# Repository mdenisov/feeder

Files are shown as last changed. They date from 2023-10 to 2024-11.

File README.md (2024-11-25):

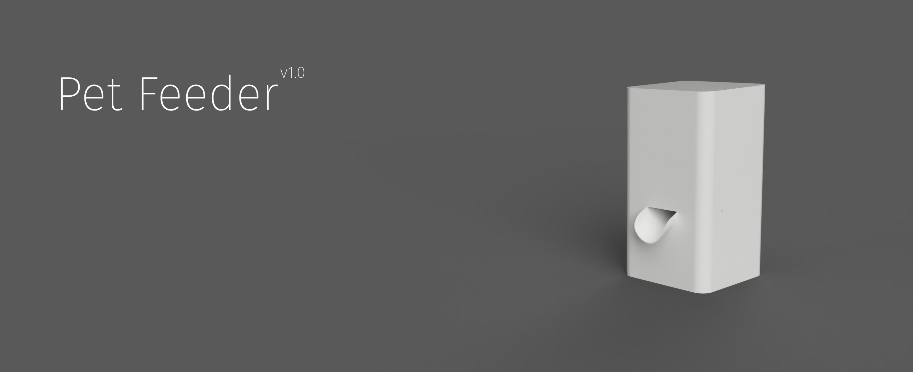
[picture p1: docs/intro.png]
Pet Feeder


# Pet Feeder

Smart feeder for pets. Works according to schedule. Supports Wifi and MQTT. WiFi remote based on ESP8266.

## Features
- Scheduled feeding
- Supports WiFi
- Supports MQTT
- Possibility of integration with a smart home

## Web Server

Feeder settings are always available on the device web page `http://feeder.local`.

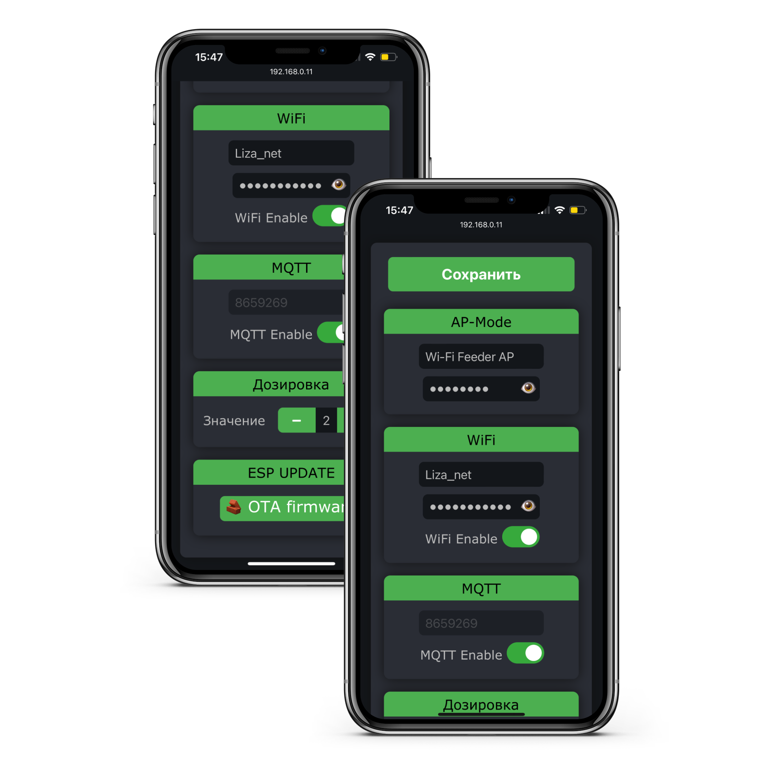
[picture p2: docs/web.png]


## Assembled device
The **STL** folder contains all the files necessary for printing.

### Reductor
Reductor designed for stepper motor **Nema 17**.
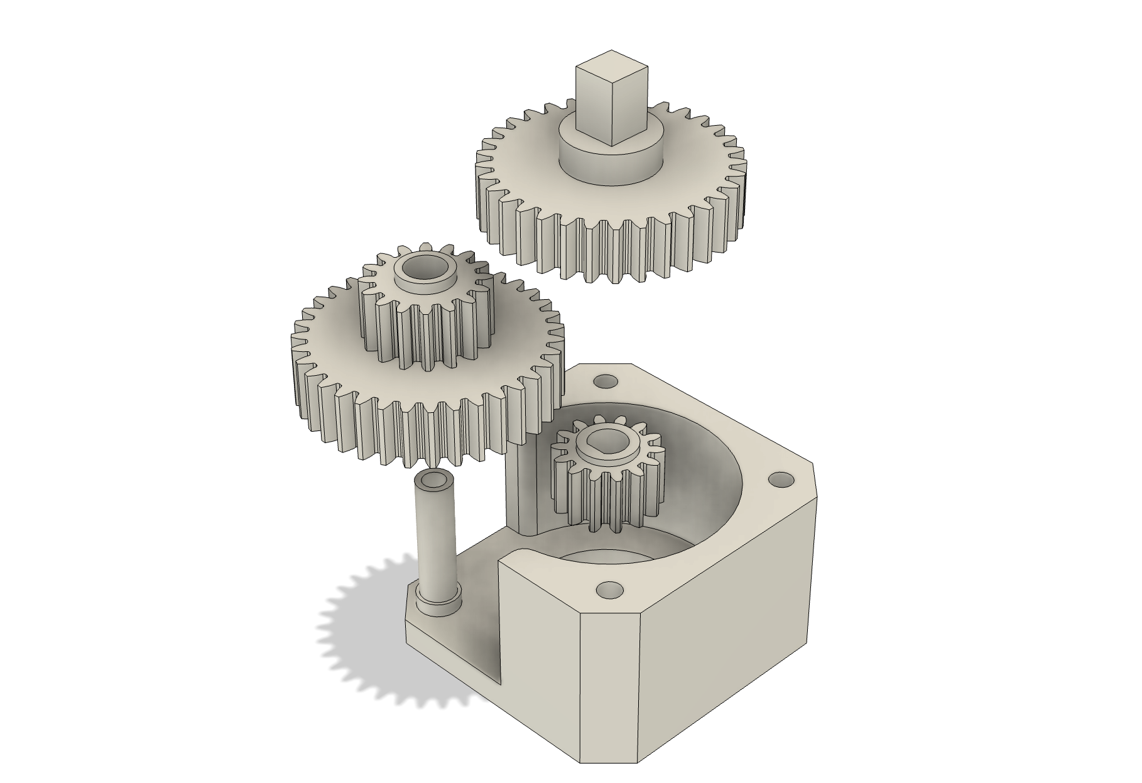
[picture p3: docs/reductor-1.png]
reductor

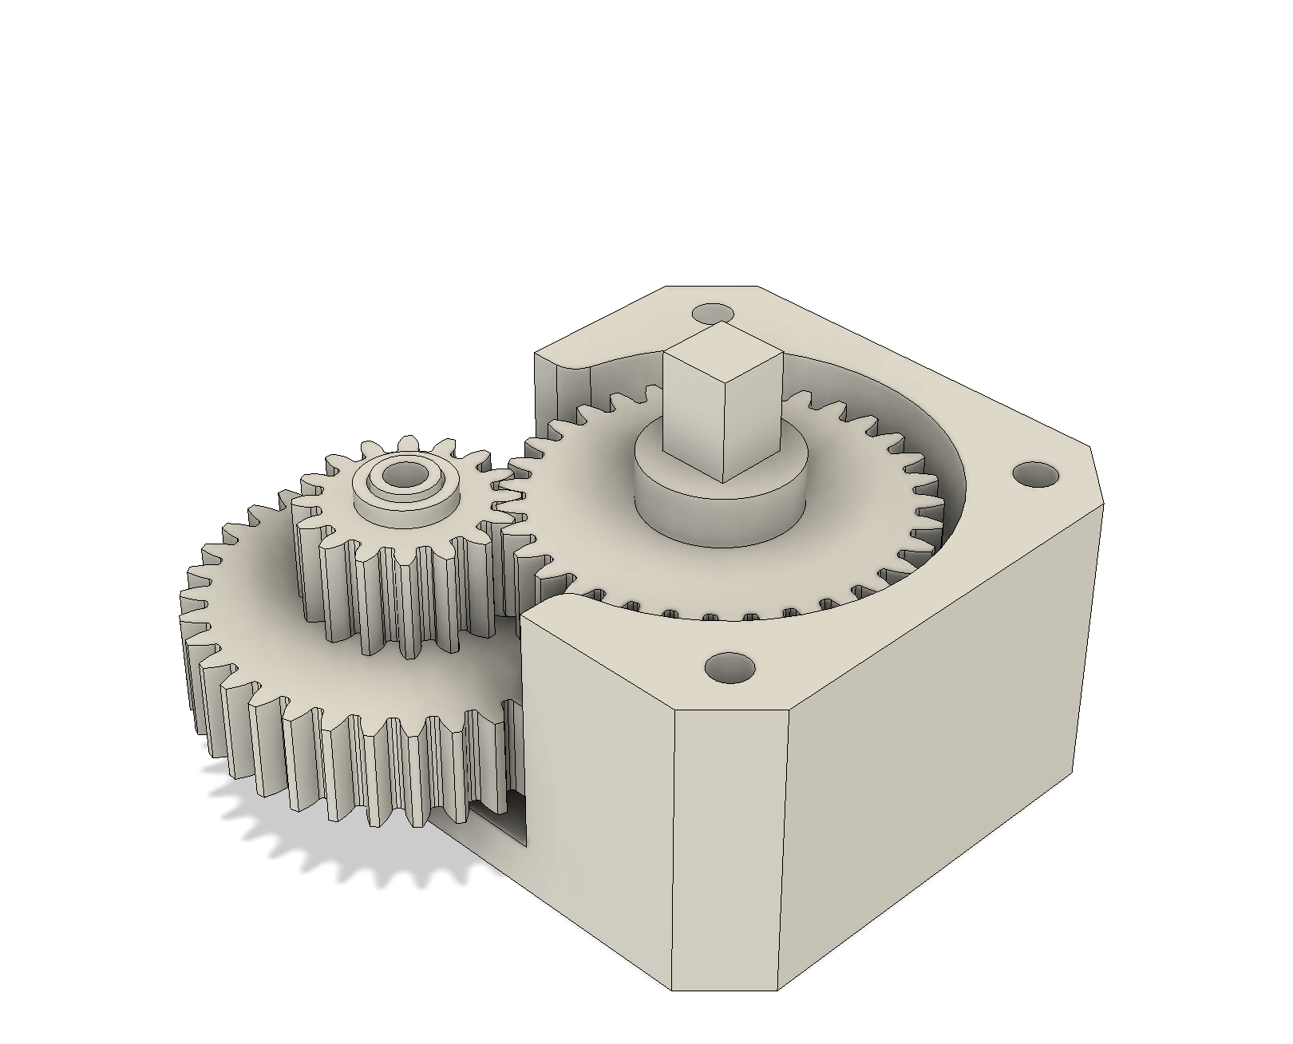
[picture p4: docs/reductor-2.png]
reductor

Use M3x30 countersunk screws to attach the reduction box to the assembly.

### Case
Step 1
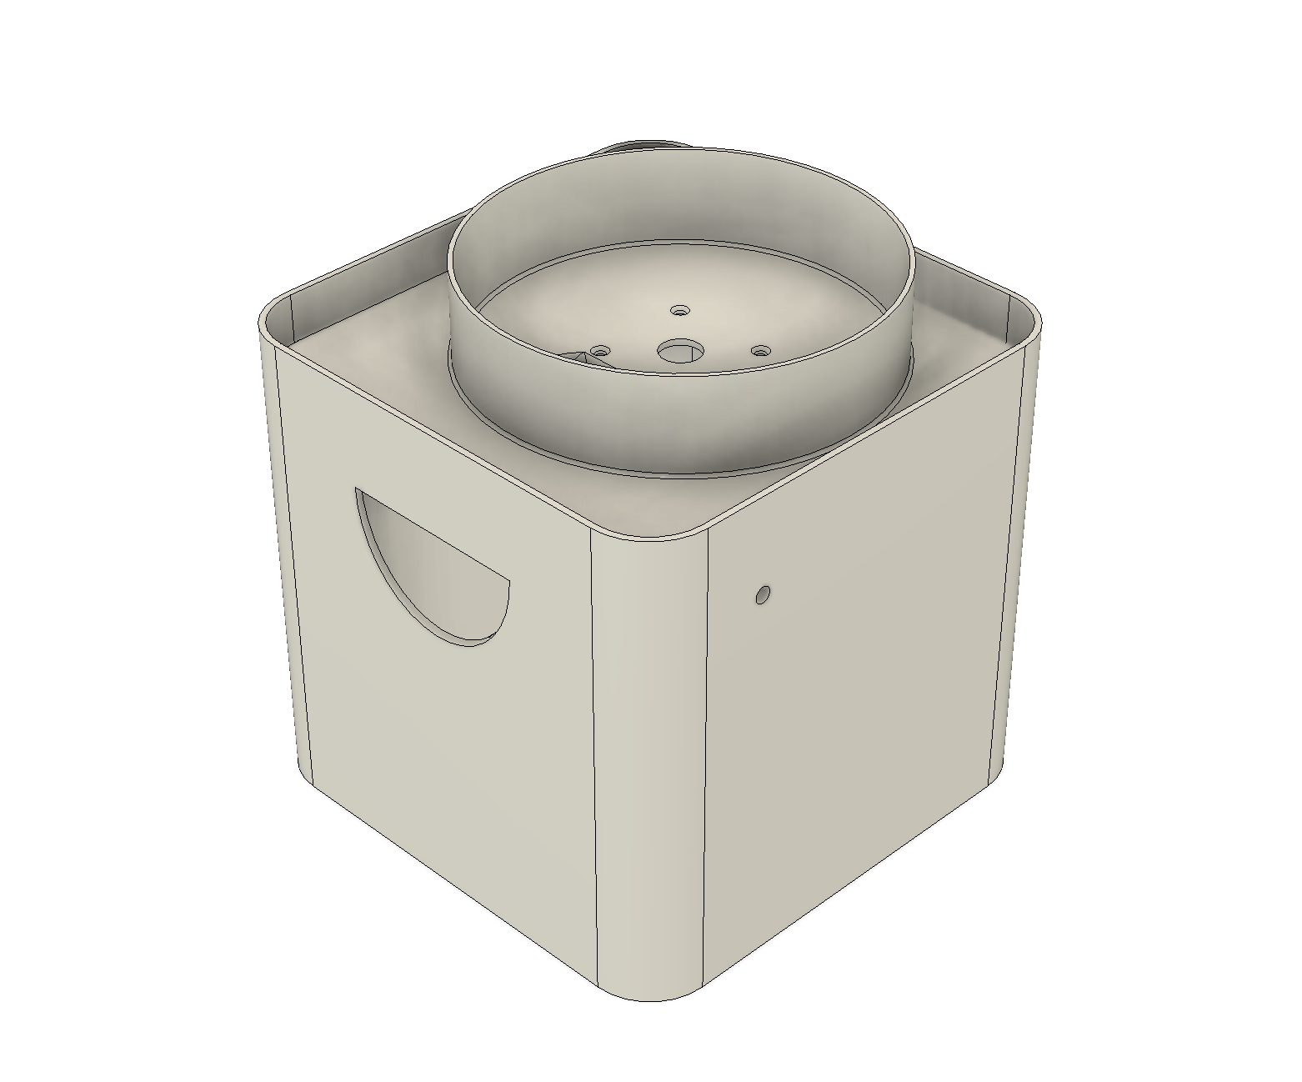
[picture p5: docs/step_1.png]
step_1

Step 2
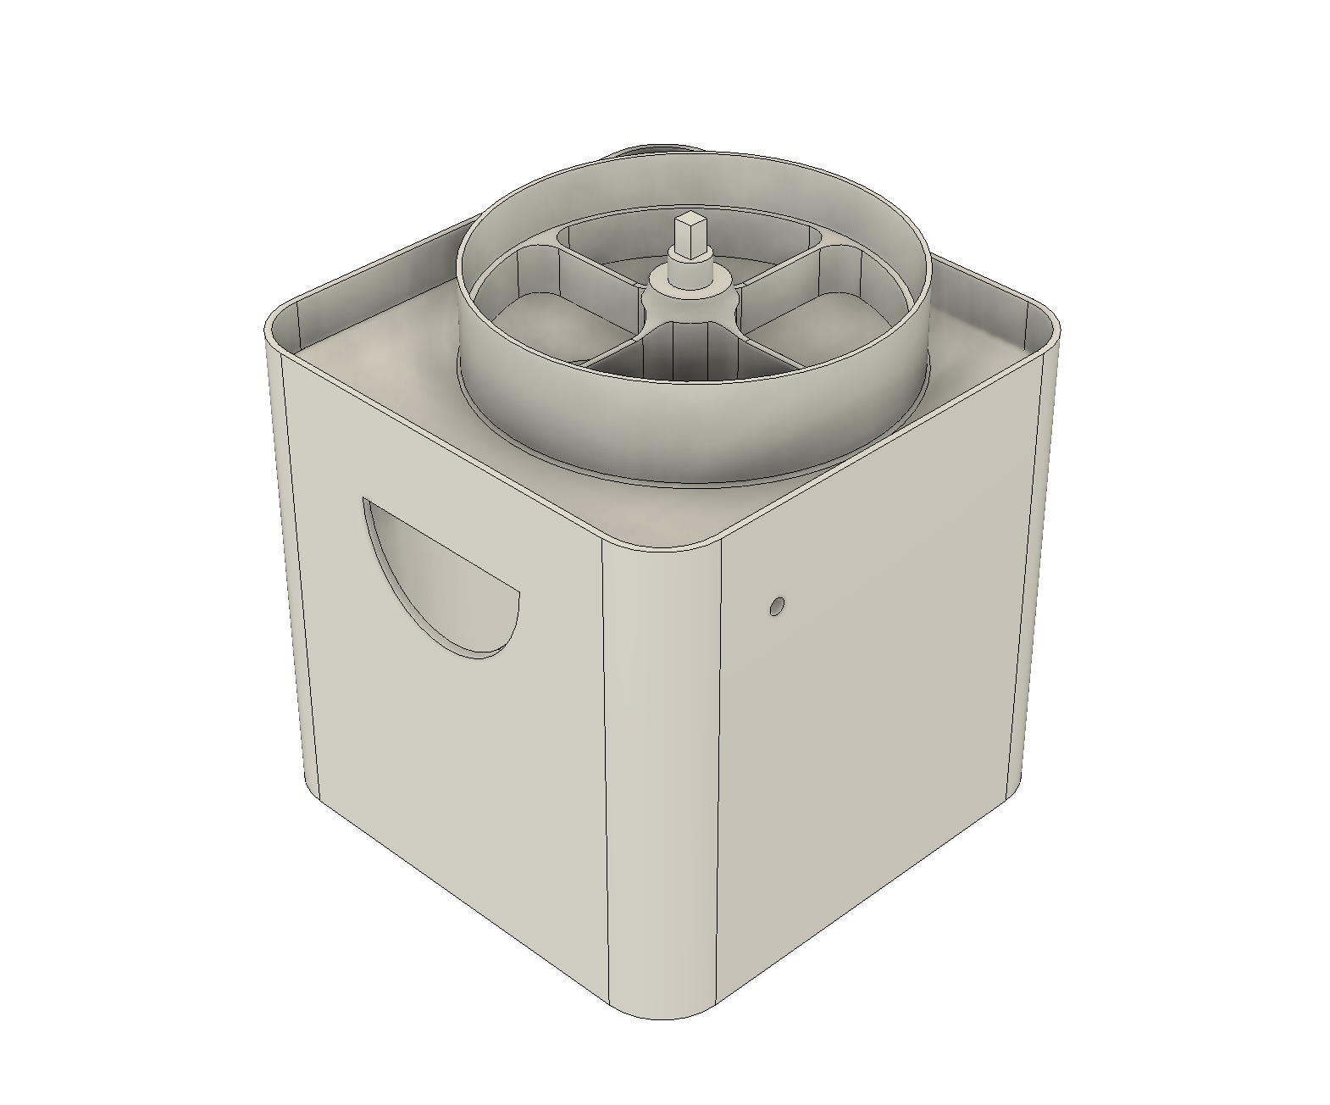
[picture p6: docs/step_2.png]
step_2

Step 3
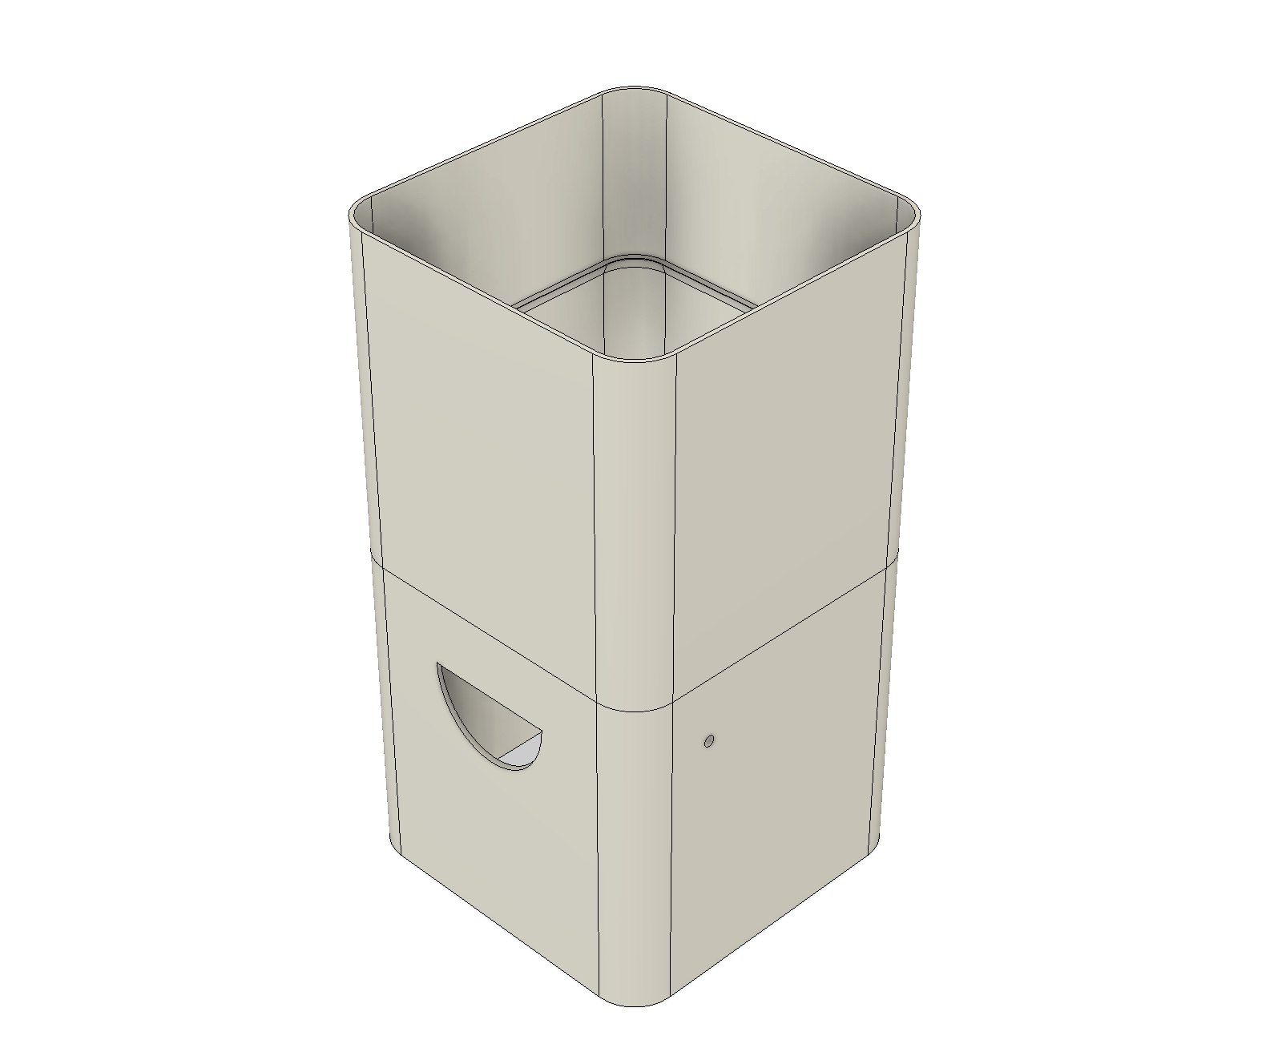
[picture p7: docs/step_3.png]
step_3

Step 4
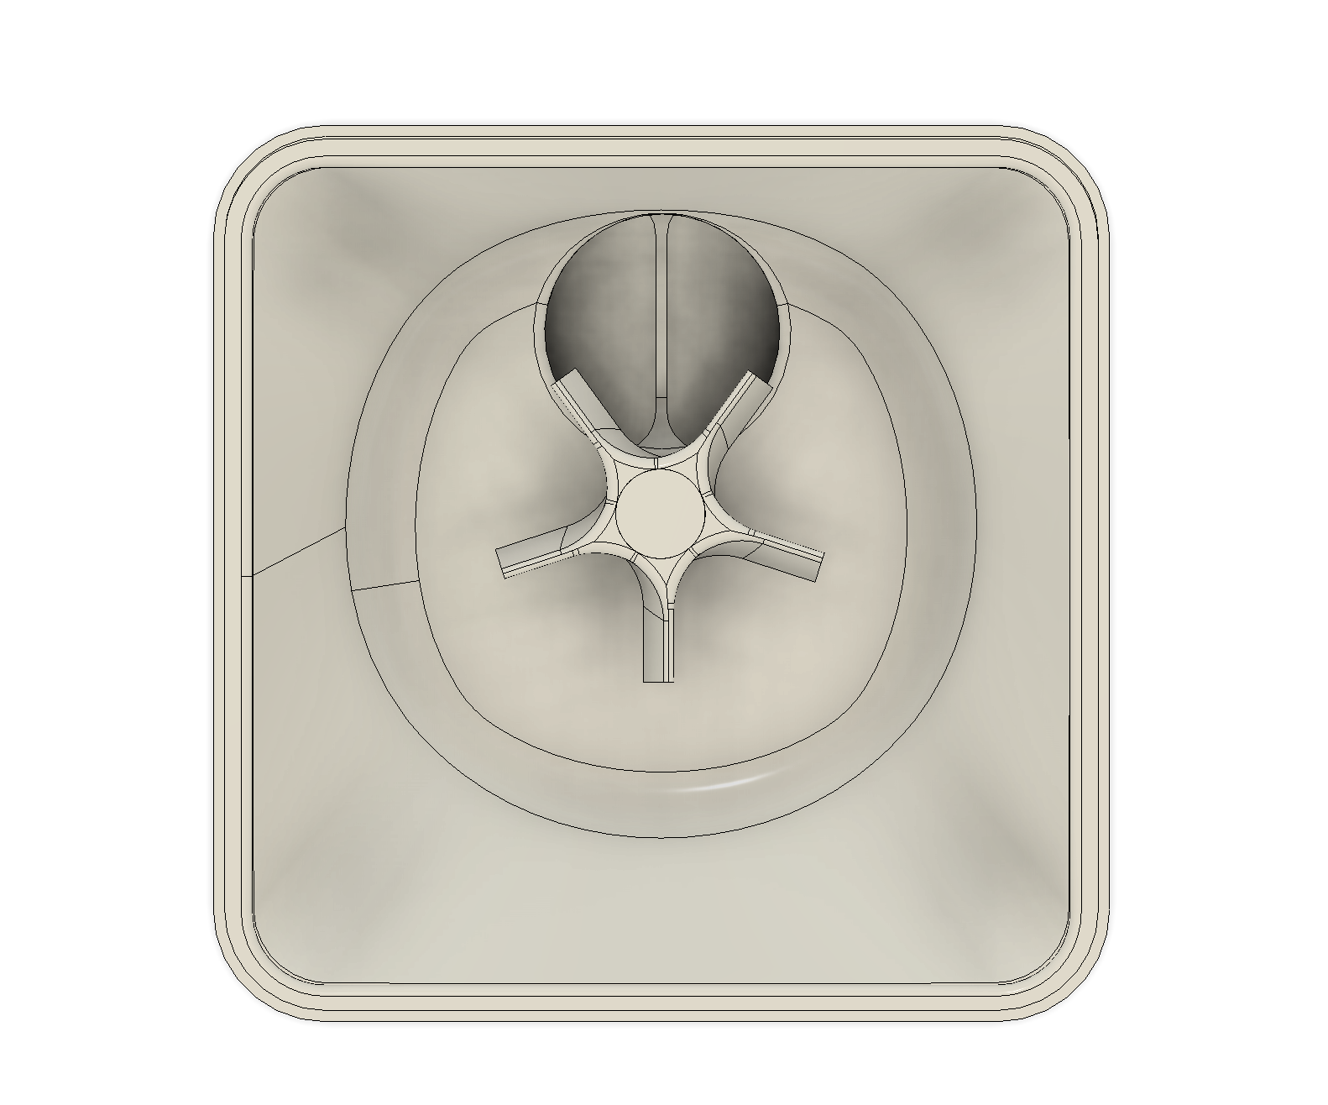
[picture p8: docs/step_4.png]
step_4

Step 5
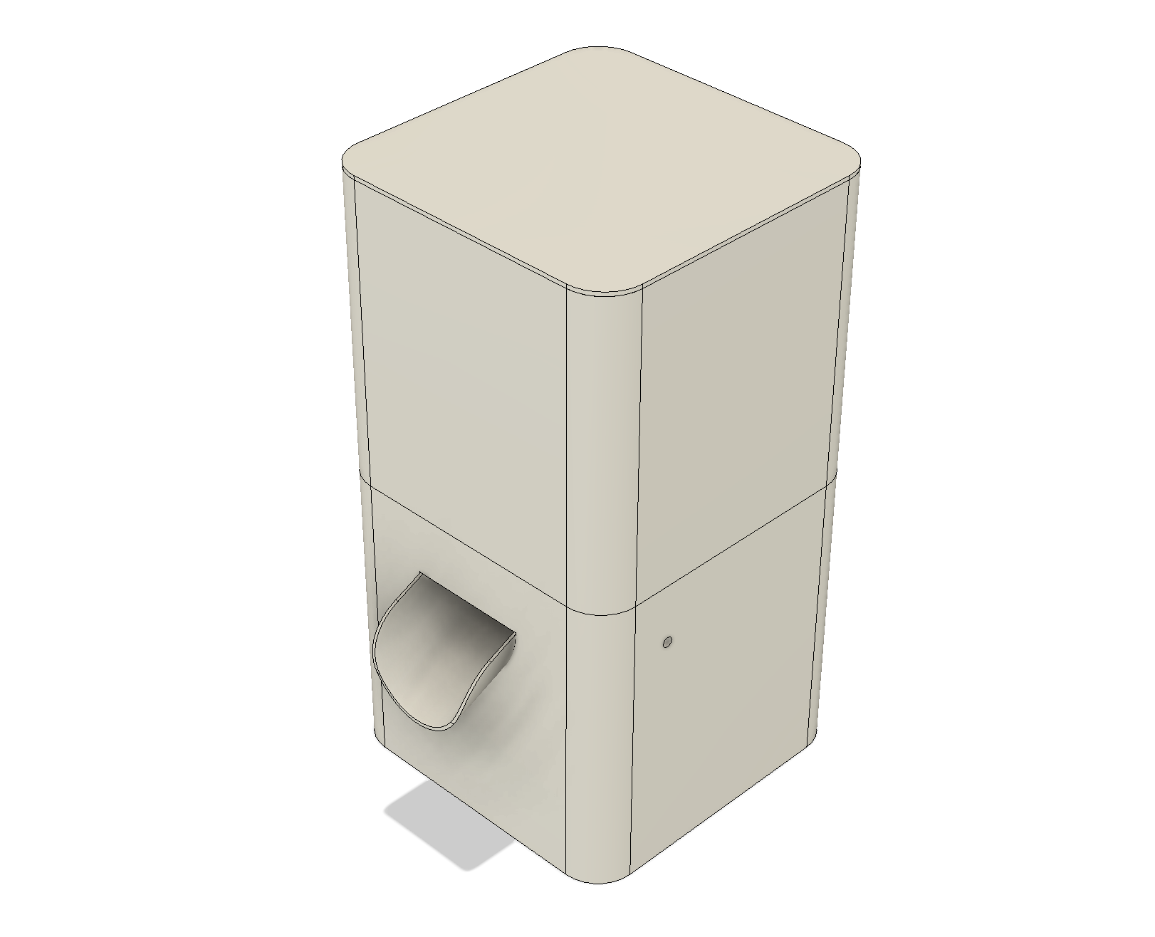
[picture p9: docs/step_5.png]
step_5

Slice
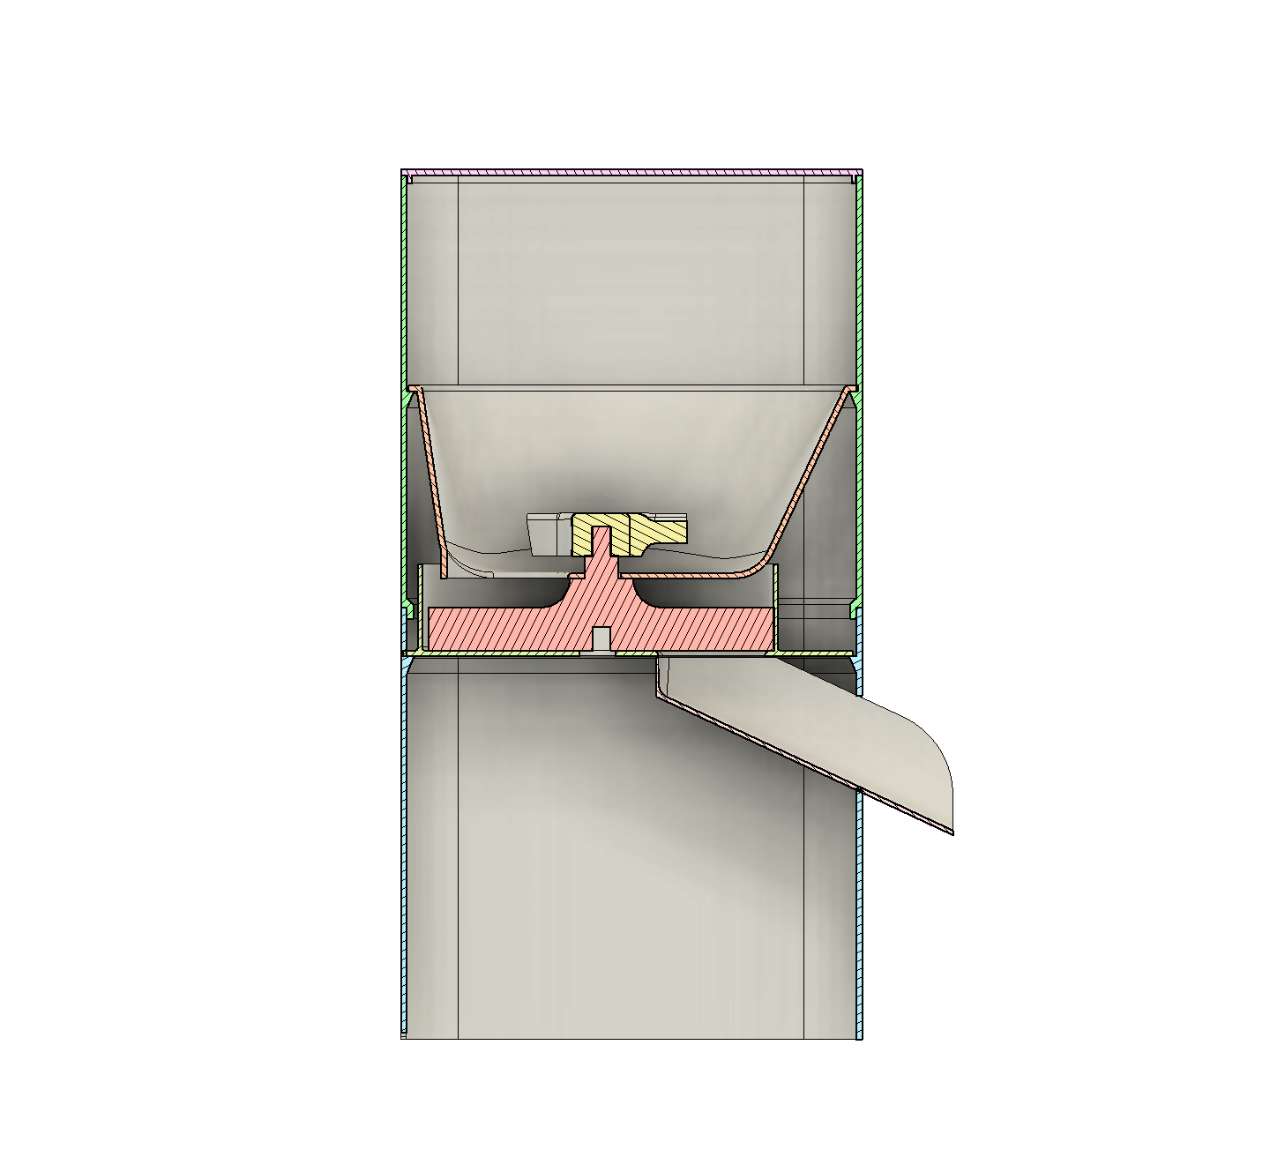
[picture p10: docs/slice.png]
slice

Final
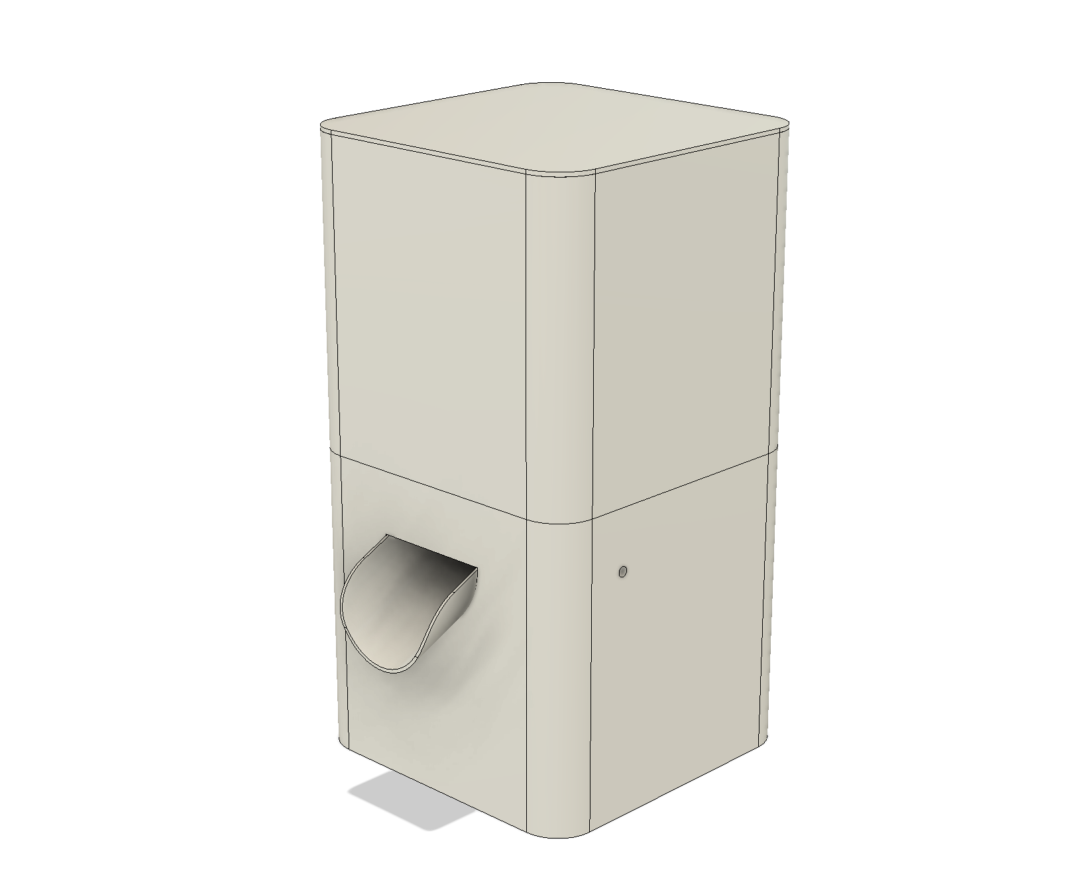
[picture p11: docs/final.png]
final


## PCB

In the **PCB** folder you will find everything you need to produce a printed circuit board.

### Main components are:

- ESP8266 (ESP-12F)
- Stepper driver A4988
- MP2307DN
- Inductor 10uH (0630; L7.0; W6.6)
- Pair diodes SS34 (SOD-123; L2.7; W1.6)
- Switch (TA-03)
- Pair JST connectors (2.0mm)
- Screw connector (KF128-2.54)
- Resistors and capacitors (0805)

And
- [Button TTP223](https://aliexpress.ru/item/32451378348.html?sku_id=66500187744)
- [Motor Nema 17](https://aliexpress.ru/item/32665922113.html?sku_id=65715688198)
- [Led](https://aliexpress.ru/item/1005004515135362.html?sku_id=12000029436349109)
- [JST Connectors](https://aliexpress.ru/item/4000091077742.html?sku_id=10000000242277758)

Final view of the printed circuit board:
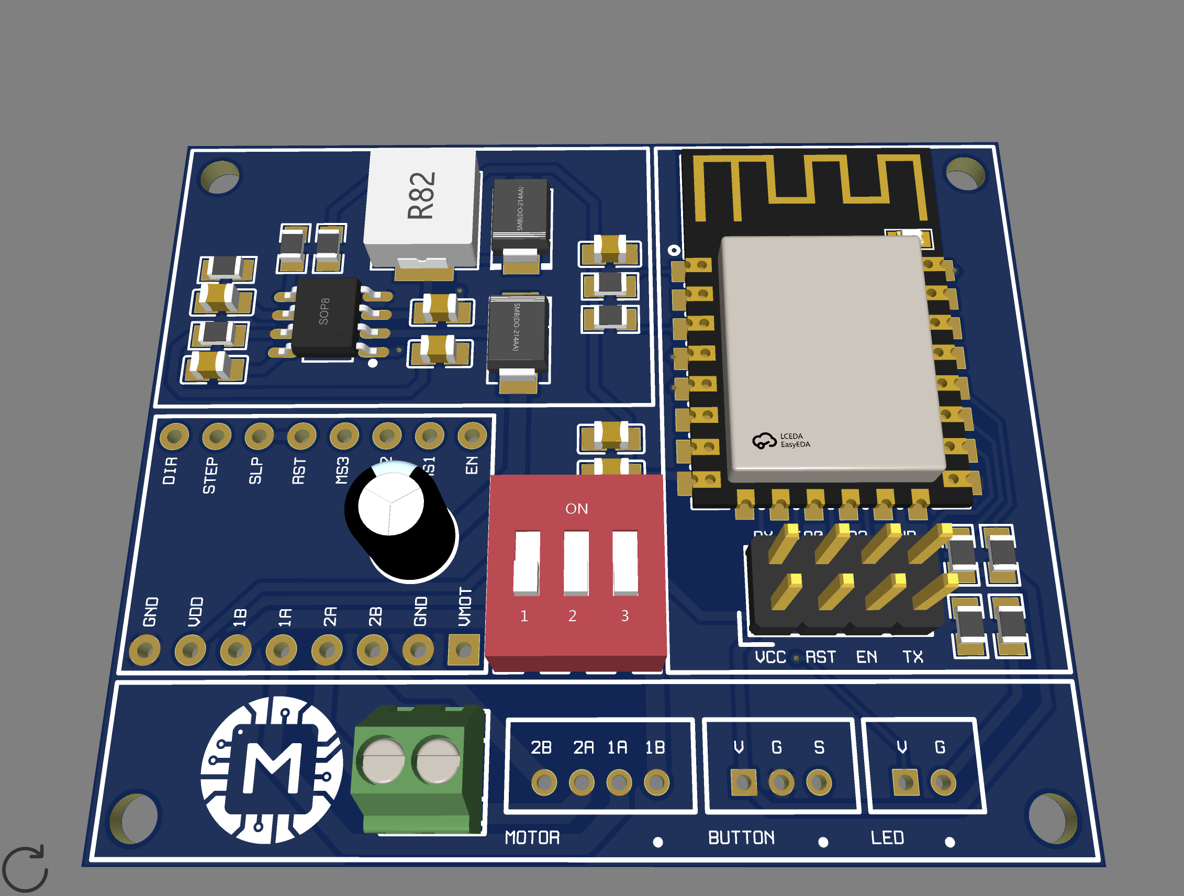
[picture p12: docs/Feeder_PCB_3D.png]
pcb


Thanks [@AlexGyver](https://github.com/AlexGyver) for awesome [libs](https://github.com/GyverLibs).

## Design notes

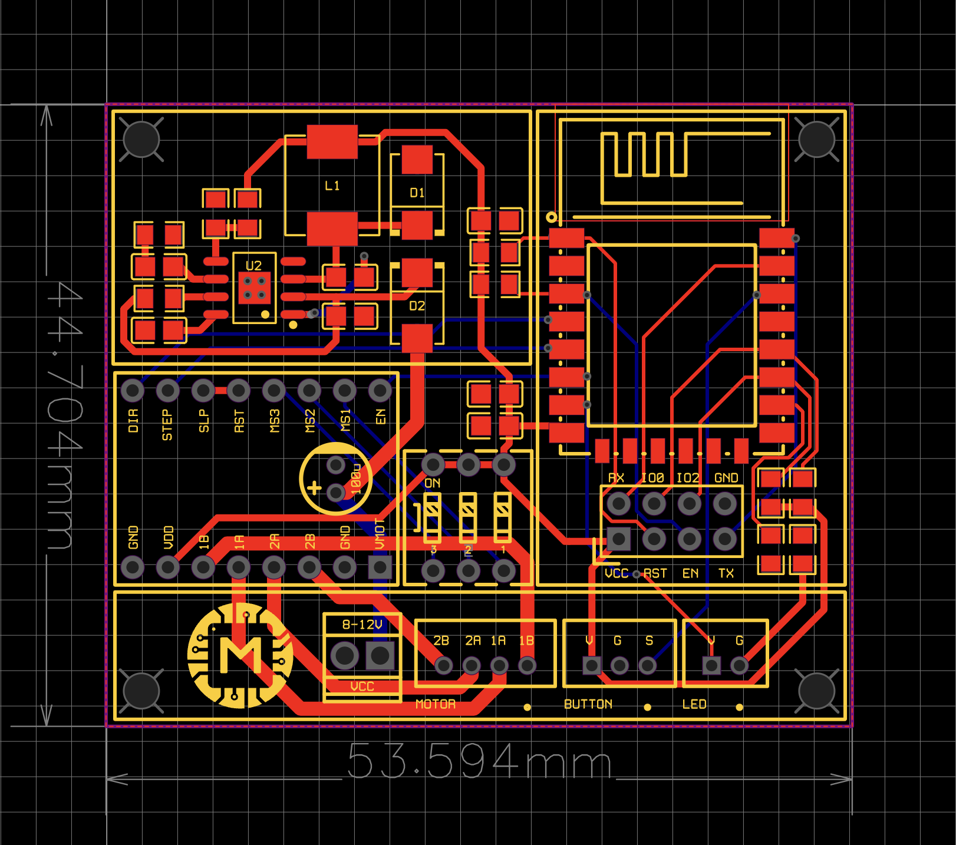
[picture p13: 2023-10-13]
docs/Feeder_PCB.png

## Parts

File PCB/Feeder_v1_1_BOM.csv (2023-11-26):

ID | Name | Designator | Footprint | Quantity | Manufacturer Part | Manufacturer | Supplier | Supplier Part
1 | MBR0530T3G | D1,D6 | SOD-123_L2.7-W1.6-LS3.7-RD-1 | 2 | MBR0530T3G | onsemi(安森美) | LCSC | C236079
2 | 100u | C1 | CAP-D5.0-F2.0 | 1
3 | 10u | C2 | C0805 | 1
4 | 100n | C3,C8 | C0805 | 2
5 | 10n | C4 | C0805 | 1
6 | 3.9n | C5 | C0805 | 1
7 | 22u | C6,C7 | C0805 | 2
8 | 1k | R6 | R0805 | 1
9 | 100k | R7 | R0805 | 1
10 | 47k | R8 | R0805 | 1
11 | 18k | R9 | R0805 | 1
12 | 6.8k | R10 | R0805 | 1
13 | 2.4GHz | U1 | WIFIM-SMD_ESP-12F-ESP8266MOD | 1 | ESP-12F(ESP8266MOD) | Ai-Thinker(安信可) | LCSC | C82891
14 | A4988 | U2 | A4988 | 1 | A4988
15 | VCC | U3 | CONN-TH_P2.54_KF128-2.54-2P | 1 | KF128-2.54-2P | KEFA(科发) | LCSC | C474920
16 | UART | U4 | UART | 1
17 | MP2307DN-LF-Z | U5 | SOP-8_L4.9-W3.9-P1.27-LS6.0-BL-EP | 1 | MP2307DN-LF-Z | MPS | LCSC | C18921
18 | 10k | R5,R4,R3,R1,R2 | R0805 | 5
19 | 10uH | L1 | IND-SMD_L7.0-W6.6_FXL0630 | 1 | FXL0624-150-M | cjiang(长江微电) | LCSC | C524609
20 | TA-03 | SW1 | SW-TH_6P-L9.2-W9.6-P2.54-LS7.62 | 1 | TA-03 | Yuandi(元迪) | LCSC | C559138
21 | LED | J1 | JST2.0_2P | 1
22 | BUTTON | J2 | JST2.0_3P | 1
23 | MOTOR | J3 | JST2.0_4P | 1

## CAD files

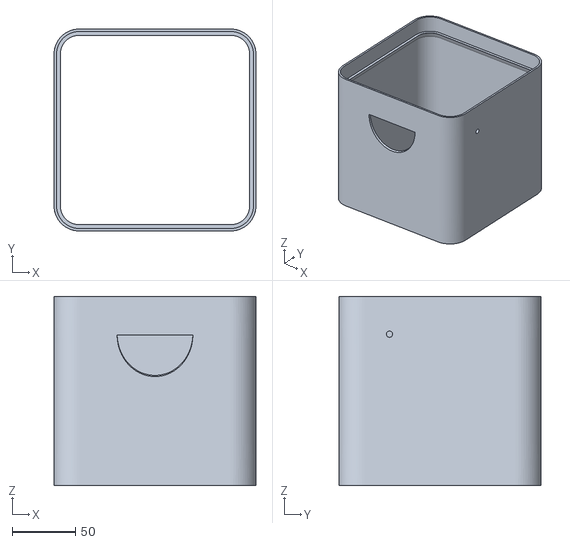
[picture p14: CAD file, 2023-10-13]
STL/box_bottom.stl
160.0 x 160.0 x 150.0

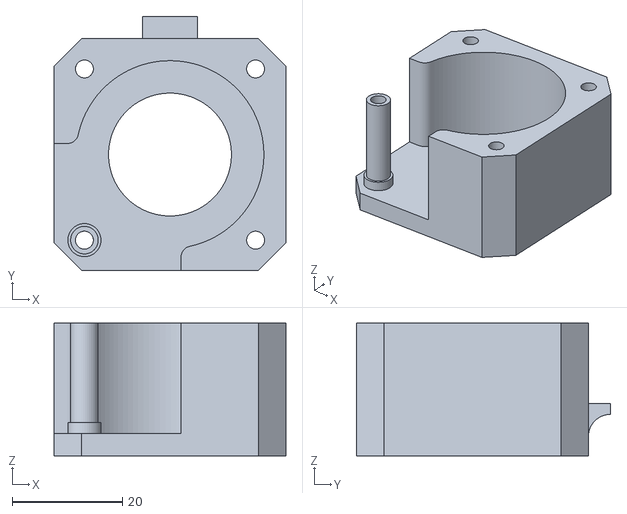
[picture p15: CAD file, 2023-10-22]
STL/reductor/reductor_box.stl
42.0 x 46.0 x 24.0

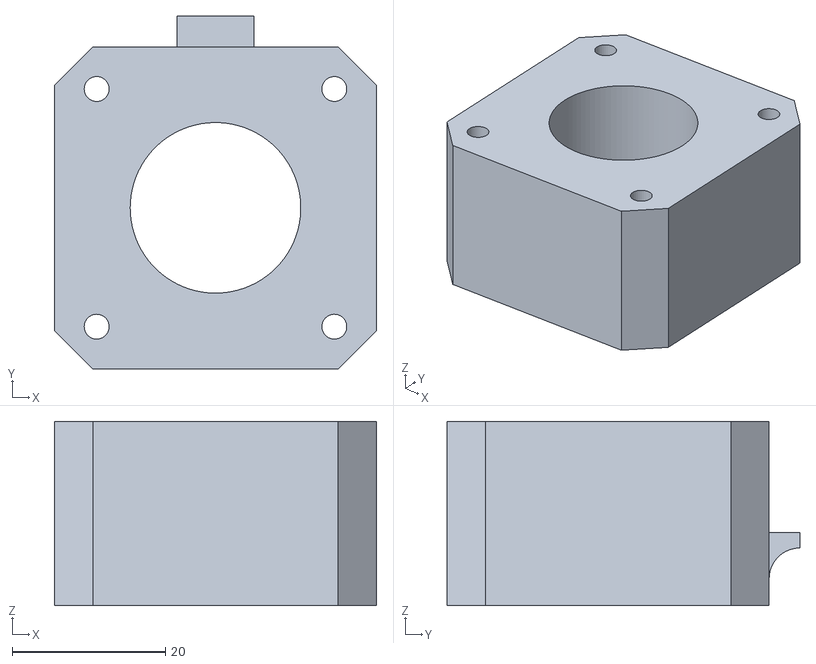
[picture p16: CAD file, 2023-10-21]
STL/without_reductor/motor_spacer.stl
42.0 x 46.0 x 24.0

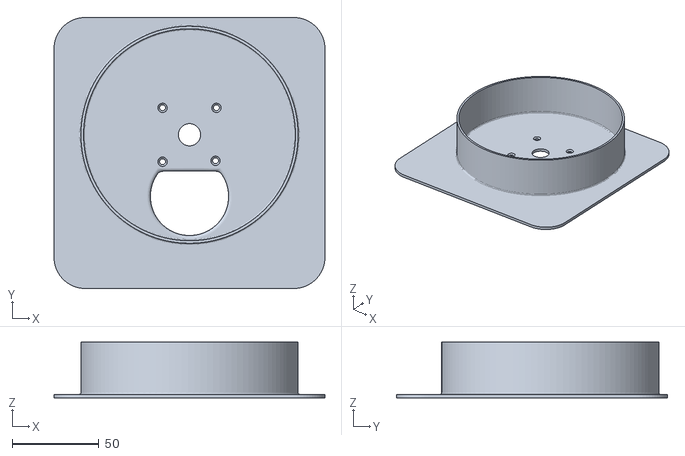
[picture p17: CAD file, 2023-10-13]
STL/box_bottom_top.stl
156.0 x 156.0 x 32.0

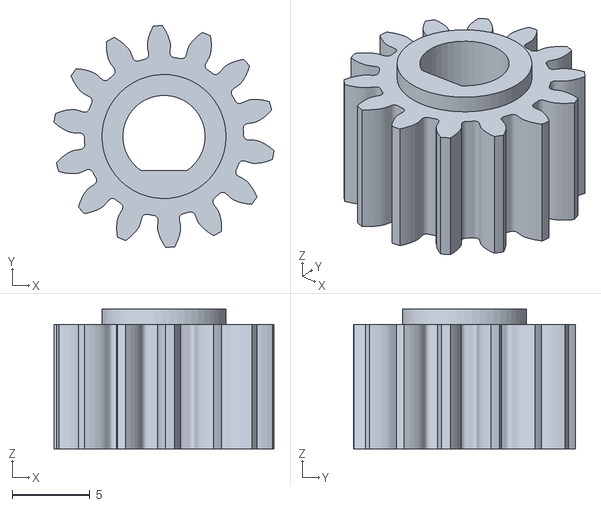
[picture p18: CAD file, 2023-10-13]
STL/reductor/reductor_gear_1.stl
14.2 x 14.3 x 9.00

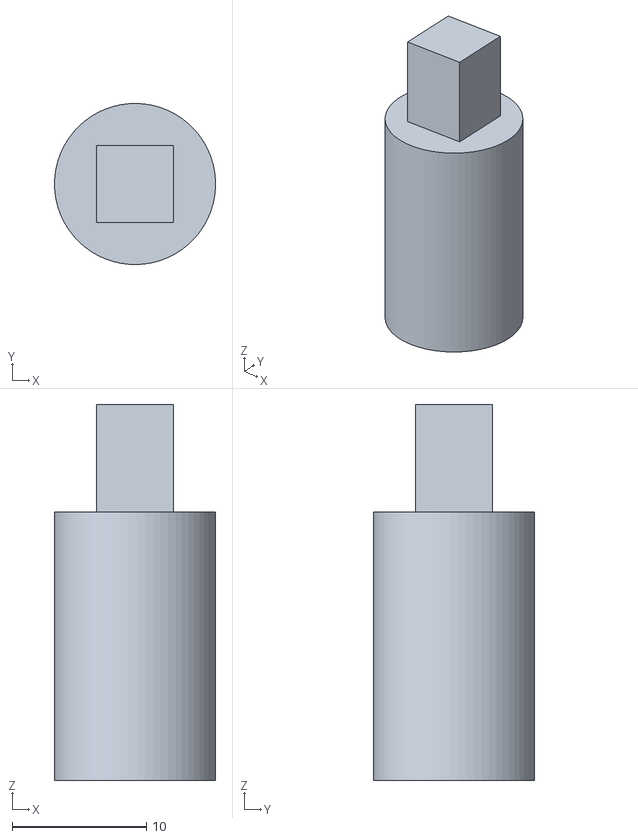
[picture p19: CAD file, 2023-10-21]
STL/without_reductor/motor_rotor.stl
12.0 x 12.0 x 28.0

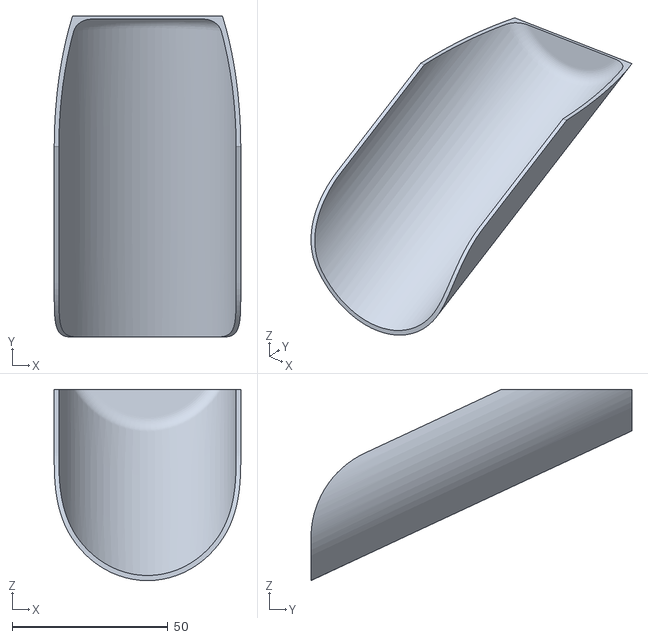
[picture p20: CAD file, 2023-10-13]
STL/box_bottom_gutter.stl
60.0 x 103.2 x 61.5

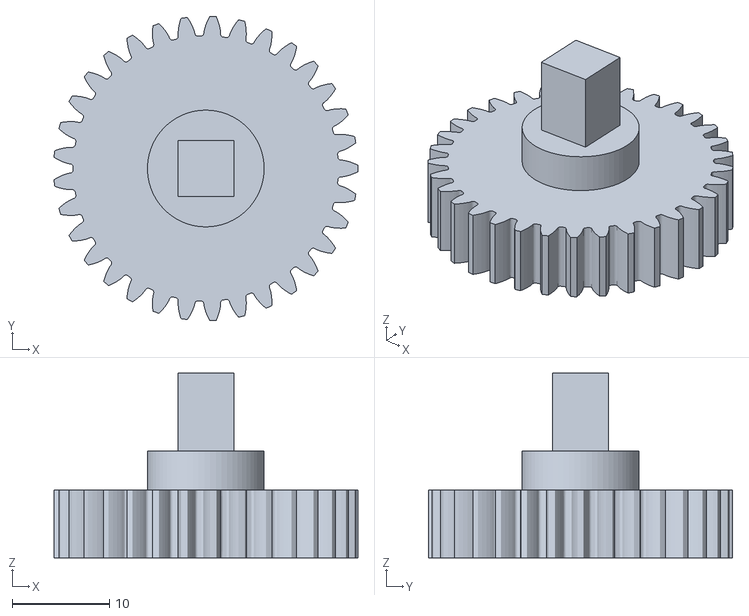
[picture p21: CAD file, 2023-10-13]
STL/reductor/reductor_gear_3.stl
31.2 x 31.3 x 19.0

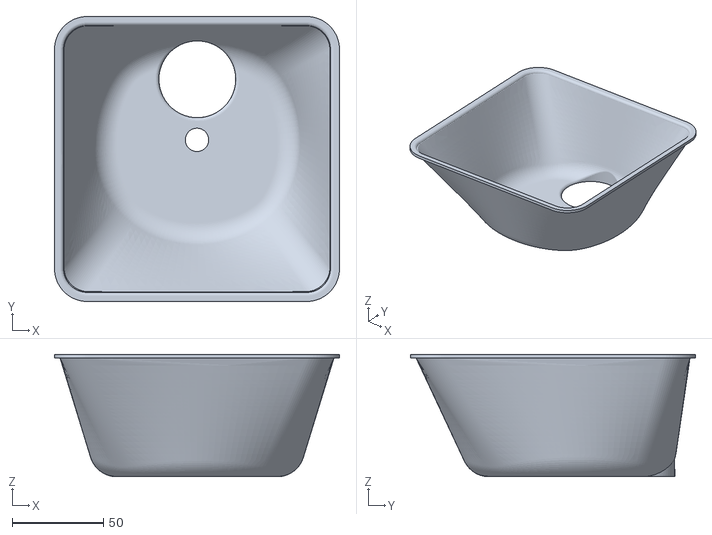
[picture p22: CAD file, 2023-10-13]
STL/box_top_crater.stl
156.0 x 156.0 x 67.0

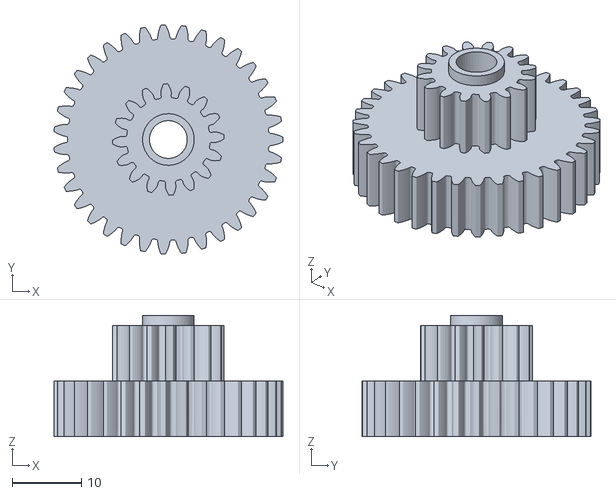
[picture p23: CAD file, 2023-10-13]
STL/reductor/reductor_gear_2.stl
33.0 x 33.1 x 17.5

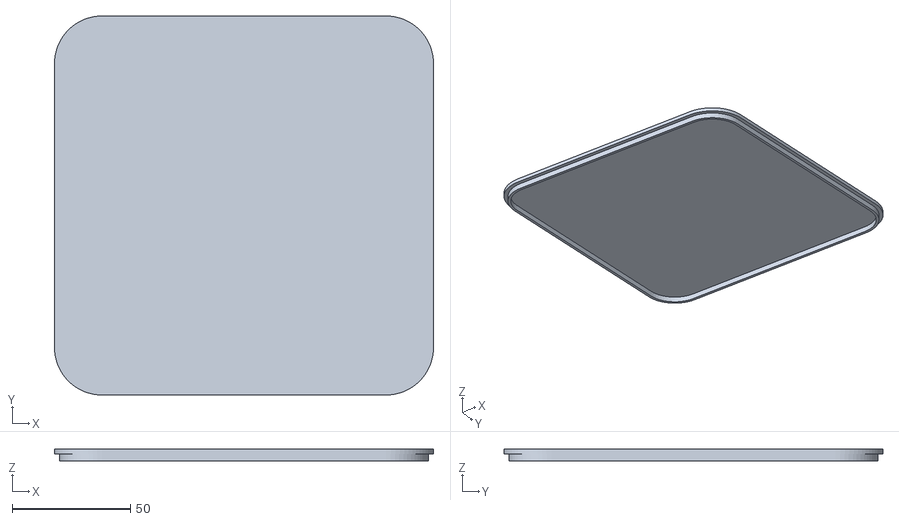
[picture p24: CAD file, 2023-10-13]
STL/box_top_cover.stl
160.0 x 160.0 x 5.00

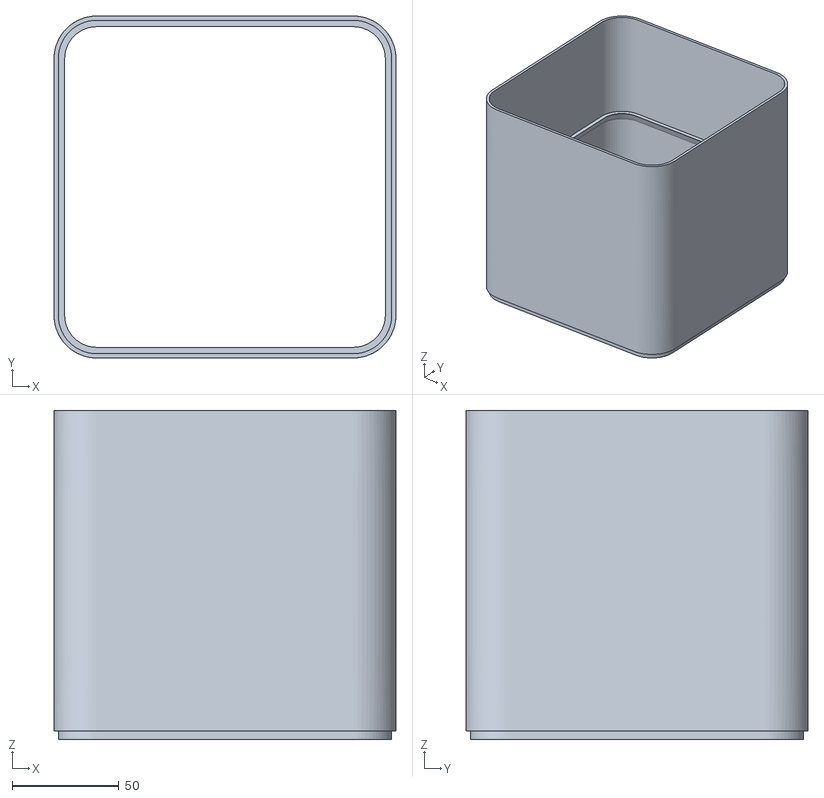
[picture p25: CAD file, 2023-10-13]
STL/box_top.stl
160.0 x 160.0 x 154.0

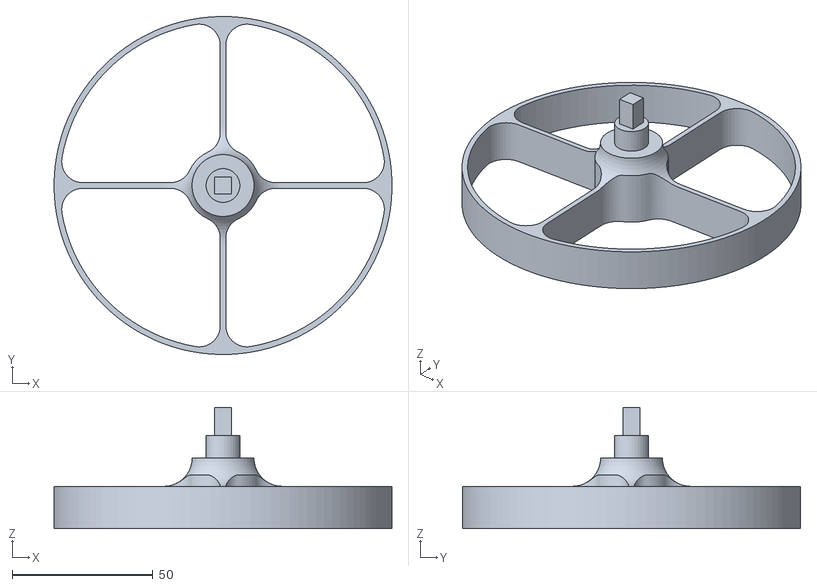
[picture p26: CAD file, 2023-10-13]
STL/box_bottom_rotor.stl
120.0 x 120.0 x 43.0

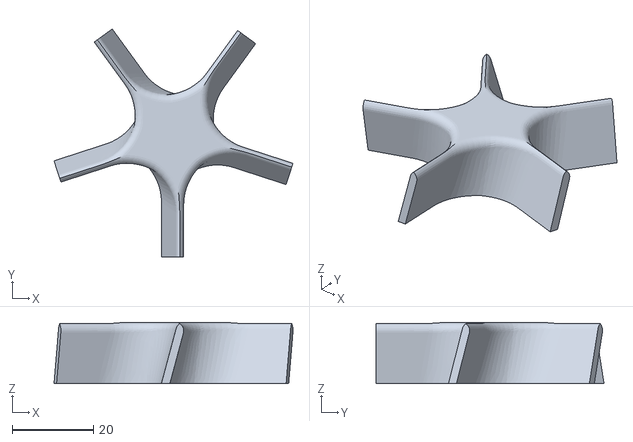
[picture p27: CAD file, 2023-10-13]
STL/box_top_screw.stl
58.8 x 56.1 x 15.0

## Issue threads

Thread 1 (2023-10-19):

Missing CPL file for PCB ordering

maksm, 2023-10-19:
Hey great project, really want to try it out, but this is my first time doing custom PCBs. I wanted to order your design on JLCPCB but in the process the BOM and CPL files are required and here in the repo only the BOM is present - could you also provide the CPL file? I have no idea what it does.

Thanks in advance and cheers for the project.

mdenisov, 2023-10-20:
@maksm Hi! To order a PCB for JLCPCB, use the included [Gerber](https://github.com/mdenisov/feeder/blob/main/PCB/Feeder_v1_0_Gerber.zip) file for upload in [order page](https://cart.jlcpcb.com/quote). I don`t have a CPL file, sorry. If you tell me how to do it, I'll do it no problem.

maksm, 2023-10-22:
@mdenisov Hey, yeah I forgot to mention that I wanted the PCB assembly also done, without it only the provided file is ok. But if I wanted to also do the PCB assembly I get to an interface where I have to provide the BOM and CPL files for the project, and am not really sure what those are.

Here is some more info when googling: https://jlcpcb.com/help/article/81-How-to-generate-the-BOM-and-Centroid-file-from-KiCAD

If I can provide any more input or help just let me know!

mdenisov, 2023-10-22:
@maksm oh, maybe you mean the element positioning file. I was able to export something like [this](https://github.com/mdenisov/feeder/blob/main/PCB/Feeder_v1_0_POS.csv). This is similar to your examples шт KiCAD.

If you need anything else, just tell me!

maksm, 2023-10-23:
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

Hey tried with the specified file, I get this error now.

```
Error

The below parts won't be assembled due to data missing.
U5,SW1,C1,C2,C3,C4,C5,C6,C7,C8,R1,R2,R3,R4,R5,R6,L1,R7,R8,J1,R9,J2,J3,D1,D2,R11,U1,U2,U3,U4 designators don't exist in the BOM file.
18K,10UH,BUTTON,3.9N,47K,UART,A4988,100N,LED,10K,100K,10N,MP2307DN-LF-Z,2.4GHZ,6.8K,100U,22U,10U,VCC,MOTOR,1K,SS34LB,TA-03,NAME FOOTPRINT QUANTITY designators don't exist in the CPL file.
```

mdenisov, 2023-10-23:
Hi 👋 Try with updated [BOM](PCB/Feeder_v1_0_BOM.csv) file. I think the error is due to a mismatch in the BOM file and Gerber file.

maksm, 2023-10-23:
Looking good now, will order 5pcs soon and report when I will assemble the unit. Might take a while :)

Thanks for all the assistance!

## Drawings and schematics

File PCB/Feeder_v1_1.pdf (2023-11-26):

MOTOR | CPU

## PULLUP

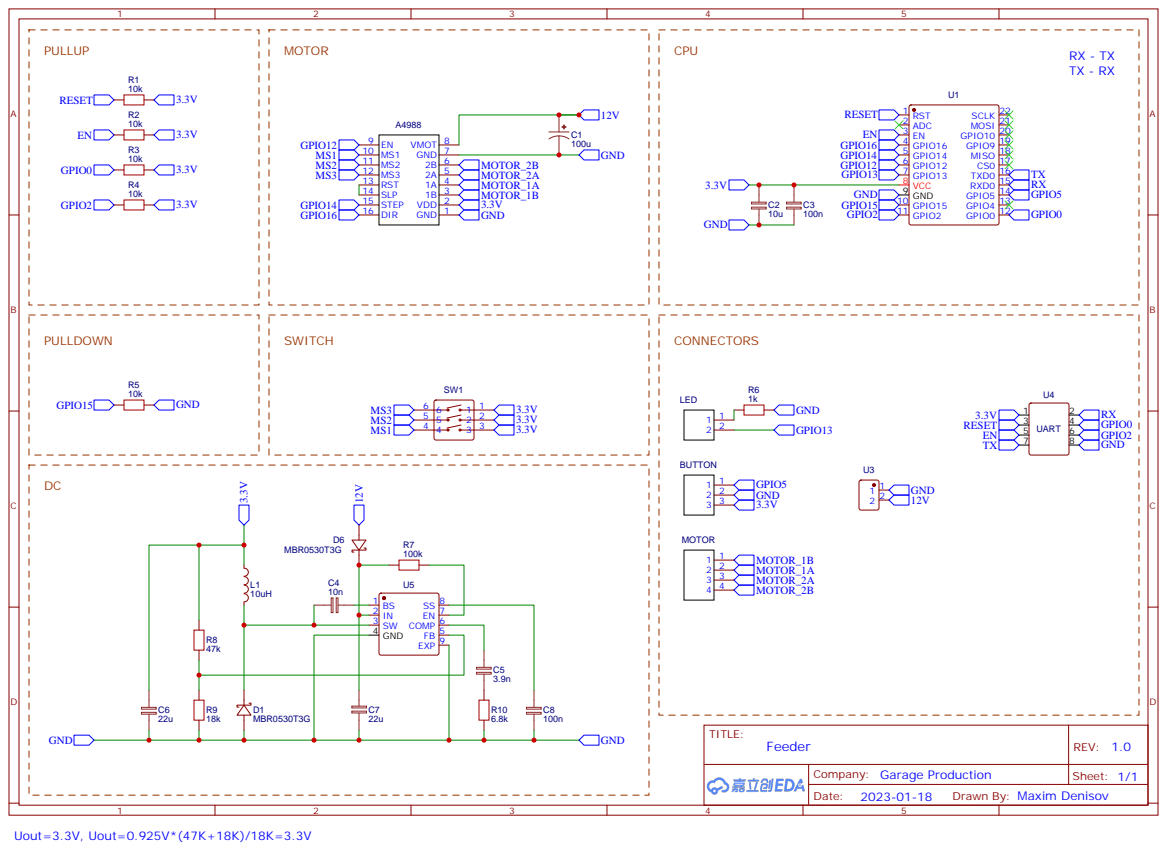
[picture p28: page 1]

Drawn By: Maxim Denisov

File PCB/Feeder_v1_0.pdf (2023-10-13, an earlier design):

MOTOR | CPU

## PULLUP

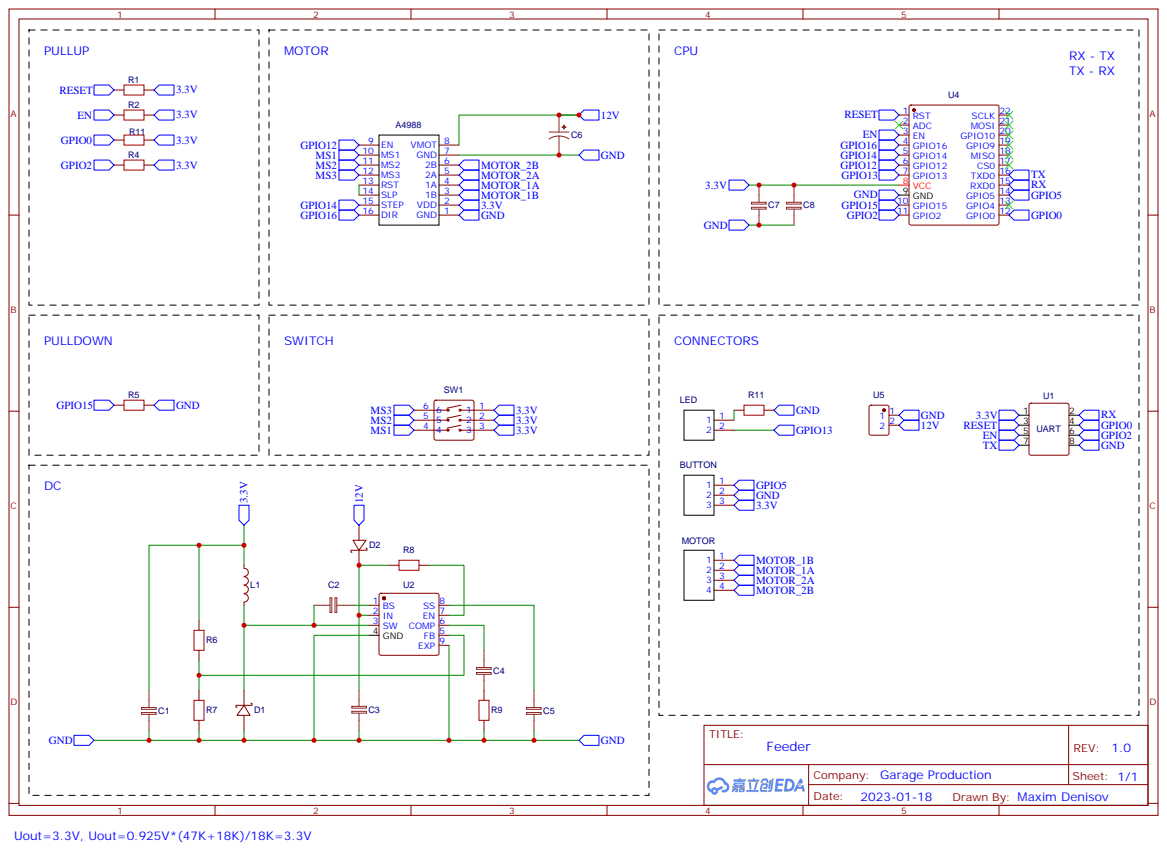
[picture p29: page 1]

Drawn By: Maxim Denisov

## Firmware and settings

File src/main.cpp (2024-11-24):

#include "env.h"

/* ================== Libs =================== */
#include <Arduino.h>
#include <EncButton.h>
#include "Led.h"

#include "config.h"
#include "utils.h"
#include "wifi-manager.h"
#include "mqtt-manager.h"
#include "eeprom-manager.h"
#include "ntp-manager.h"
#include "stepper-manager.h"
#include "schedule-manager.h"
#include "web-server.h"

/* ================ Objects ================== */
Button btn(BTN_PIN, INPUT_PULLUP, HIGH);
Led led(LED_PIN);

/* ================== Main =================== */
void setup()
{
#ifdef DEBUG_MODE
  Serial.begin(115200);
#endif

  pinMode(BTN_PIN, INPUT_PULLUP);

  led.begin();
  led.on();
  initEEPROM();
  initWifi();
  initMQTT();
  initNTP();
  initStepper();
  initSchedule();
  initUI();
}

void loop()
{
  btn.tick();
  led.tick();
  loopNTP();
  loopMQTT();
  loopStepper();
  loopSchedule();
  loopUI();

  if (btn.hasClicks(2))
  {
    feed();
  }

  if (btn.hasClicks(3))
  {
    DEBUGLN(F("Button click 3 times"));

    appState.isStucked = true;
  }

  // Led
  if (appState.isFeeding)
  {
    led.blink(5);
  }
  else if (WiFi.status() != WL_CONNECTED)
  {
    led.smooth();
  }
  else
  {
    led.on();
  }
}

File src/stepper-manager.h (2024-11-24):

#ifndef _STEPPER_MANAGER
#define _STEPPER_MANAGER

#include <Arduino.h>
#include <GyverStepper2.h>
#include "env.h"
#include "config.h"
#include "utils.h"

GStepper2<STEPPER2WIRE> stepper(STEPPER_STEPS * STEPPER_MICRO_STEPS, STEP_PIN, DIR_PIN, EN_PIN);

const int feedAmount = (STEPPER_STEPS * STEPPER_MICRO_STEPS * STEPPER_GEAR_RATIO) / 4;

void feed()
{
  if (!stepper.tick())
  {

    DEBUGLN(F("Feeding"));

    // publishMessage(MQTT_TOPIC_FEED_STATUS, "1", false);
    stepper.reset();
    stepper.setTarget(feedAmount * config.dosage, RELATIVE);
  }
}

void initStepper()
{

  DEBUGLN(F("Init Stepper"));

  stepper.setMaxSpeed(2300);
  stepper.setAcceleration(3500);
  // stepper.reset();
  stepper.autoPower(true);
  stepper.disable();
}

void loopStepper()
{
  if (stepper.tick())
  {
    appState.isFeeding = true;
  } else {
    appState.isFeeding = false;
  }

  static int shakeAttempts = 0;
  if (stepper.ready())
  {
    if (appState.isStucked)
    {
      if (shakeAttempts == 0) {
        stepper.setTarget(-1, RELATIVE);
      }

      if (shakeAttempts < 10)
      {
        bool dir = shakeAttempts % 2;
        stepper.setTarget(dir ? 500 : -500, RELATIVE);
        shakeAttempts++;
      }
      else
      {
        shakeAttempts = 0;
        appState.isStucked = false;
        feed();
      }
    }
    else
    {
      // publishMessage(MQTT_TOPIC_FEED_STATUS, "0", false);
    }
  }
}

#endif

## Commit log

2023-10-13 Add PCB and schemas
2023-10-13 Add STLs
    [box_bottom.stl, box_bottom_gutter.stl, box_bottom_rotor.stl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]
2023-10-22 Update logic
    [reductor_box.stl]
2023-10-22 Add POS file
    [Feeder_v1_0_POS.csv]
2023-10-23 Update BOM file
    [Feeder_v1_0_BOM.csv]
2023-11-26 Update PCB
    [Feeder_v1_1_BOM.csv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]
2024-06-20 Update gerber
